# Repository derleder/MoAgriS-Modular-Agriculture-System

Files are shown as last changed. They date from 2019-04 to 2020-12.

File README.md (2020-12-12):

# MoAgriS - Modular Agriculture System

## Introduction
MoAgriS is a System to automate plant care with the help of modules for light, water and wind. The modules are plugged onto 3 rods providing power and communication. This way they can be placed individually to fit the plants needs. The project has been developed under Windows but the use of Linux is possible and encouraged.

## Quickstart
There is none. You need to get the PCBs and the components of the [BOM](#bom) first and combine them yourself or let your provider populate everything. [LCSC](https://lcsc.com/) has been quite usefull since they offer a [PCB service](https://jlcpcb.com/) besides the components and the shipment can be combined. A possible PCB configuration can be seen in [PCB/notes/pcb-spec.PNG](./PCB/notes/pcb-spec.PNG). The default values such as PCB thickness or copper weight of 1 oz are fine, too. Unfortunately not all parts can be found there at the time of writing such as the SAMD11 or the PT4115 current regulator.

Once a PCB is ready the SAMD11 needs a [bootloader](https://github.com/mattairtech/ArduinoCore-samd/blob/master/bootloaders/zero/binaries/sam_ba_Generic_D11C14A_SAMD11C14A.bin) by [Mattairtech](https://github.com/mattairtech) to be transmitted via the SWD interface. This is a one-time procedure since the bootloader handles all the firmware updates via USB afterwards. The [Segger J-Link](https://www.segger.com/products/debug-probes/j-link/models/j-link-edu-mini/) comes in handy for that if the licensing is not a problem to you. Other solutions are possible as long as the SAMD11 is supported. Currently I use [Atmel Studio](https://www.microchip.com/mplab/avr-support/atmel-studio-7) for this step (Tools->Device Programming) though the Studio is quite an overkill.

Right now there is no Firmware binary (see [Future](#Future)) so you need to go through the [Development](#Development) section to set up the [Arduino IDE](https://www.arduino.cc/en/main/software). After that you can compile and upload the firmwares found in [Firmware](/Firmware). You need one master on the SDI bus and you can use pretty much as many slaves as you want - tell me if there's a limit. The master can be any PCB that has a SAMD11 if you wish to wish keep your order small. The dedicated master PCB only has power and BUS connectors.

Now that the PCBs are fully working it's time to clamp them on the rods. Plug the master via USB into your PC/Raspberry and open a serial console such as Realterm (Windows) or minicom (Linux). Find out the masters COM-Port (Windows: Device Manager -> COM & LPT ports -> the one thats containing Mattairtech in the description), set the Baud rate to 115200 and connect to it. You should receive a welcoming "Opening SDI-12 bus master..." the first time you connect to the master. It's best to tell your terminal to add a line feed (\n) to a command. This way the master knows to send it over the SDI bus - it's not neccessary since a command is sent anyway after a timeout of 1s.

That's it pretty much. You should be able to send commands to the individual modules now. There's a node-red solution in development to automate it further.

## Alternative Uploading
Since the USB ports are no real benefit they can be left out except for the master board which uses it for serial communication. To achieve that choose [NO_BOOTLOADER in the Arduino Tools Bootloader size menu](https://github.com/mattairtech/ArduinoCore-samd#bootloader-size-menu). After you created/exported the binaries you can use another programmer like Atmel Studio to program directly via the Segger J-Link to the very start of the flash (no address needs to be specified).

The binaries can also be found directly in the corresponding folders under Firmware.

## Development
Thanks to [Mattairtechs ArduinoCore-samd](https://github.com/mattairtech/ArduinoCore-samd) firmware development is quite easy. The setup is described [here](https://github.com/mattairtech/ArduinoCore-samd#installation) (two parts!). The flash size of the SAMD11 is quite small to fit in all the firmware but it is possible if you turn off as many functions as possible in the config.h (Windows: C:\Users\User\AppData\Local\Arduino15\packages\MattairTech_Arduino\hardware\samd\1.6.18-beta-b1\config.h). My config can be found in [Firmware/config.h](./Firmware/config.h). You will save additional flash space by setting serial config under tools to "no_uart_one_wire_one_spi".

You also need to install [Arduino-SDI-12](https://github.com/EnviroDIY/Arduino-SDI-12/releases/tag/v1.1.0) and add it to the Arduino IDE for the <SDI12.h> include. Please use v1.1.0 since newer ones do not seem to work with the SAMD11.

Additionally you should avoid costful code such as the String datatype. Right now the complete firmware for the slave takes up 10232 Bytes.

## SDI Commands
The SDI protocol consists of commands from the master and answers from the sensors in printable 7bit ACII characters. A command starts with an [address](#Addressing) followed by an instruction and an optional parameter. It is finished with an '!' and sent to the module(s). If the command is a heartbeat or a group instruction the module doesn't answer. If a certain module is addressed the answer will be given via the SDI bus starting with its address and an answer. That string is also printed to the serial if you connected the module via USB for debugging purposes.

### Addressing
The modules are addressed by a 4 character lower case hex string which represents two bytes of an SDI address. It is created during bootup in the module by xoring the 3 serial number registers of the SAMD11. Since there is no EEPROM on the controller this seems to be the best solution for getting almost unique addresses. When you install the firmware you should set up a one master one slave system to get the modules address by '?I!' and write it somewhere like the left out rectangle on the module.

Besides addressing a single module you can address multiple ones with a single command. That way you won't receive any answers from the modules though - the master will always send "ACK". The wildcard character '?' will address all modules. If an single upper case letter is used you can address groups. The default group is 'N' as in None. You can set the group of a module by sending 'abcdGL!' ('abcd' = address, 'G' = set group, 'L' = Group L). Remember there is no EEPROM so the group will be lost once the module reboots. Either write a setup routine or set SDIGROUPDEFAULT in the firmware code to keep the group after booting.

### Instructions
Commands should be finished with \n and responses are finished by \r\n by the module itself.

| Instruction | Description | Answer | Example (Command!Response) |
| --- | --- | --- | --- |
| I | Identification | abcd | ?I!abcd |
|||(Address)||
| V | Version | 00.00.02 | abcdV!abcd00.00.02 |
|||(Version)||
| Ccccc | Change address | [new Address] | abcdC1234!1234 |
|| cccc: Address |||
| H | Send Heartbeat to avoid module returning to a save state| - | ?H! |
| Jiiii | Set heartbeat interval | ACK | abcdJ0060!abcdACK |
|| iiii .. Interval in seconds (trailing 0s)
| Gc | Set SDI group | ACK | abcdGL!abcdACK
|| c: Group
| K | Get SDI group | [Group] | abcdK!abcdL
| Si | Set status LED | ACK | abcdS0!abcdACK
|| i: 0 (on), 1 (off) 
| Liii | Set power LED | ACK | abcdL100!abcdACK
|| iii: 000..255 (trailing 0s) || LL255!
| Pi | Set pump | ACK | abcdP1
|| i: 1(on), 0(off)
| Fiii | Set fan | ACK | abcdF100!abcdACK
|| iii: 000..255 (trailing 0s)

## BOM
The [BOM /PCB/notes/BOM.ods](./PCB/notes/BOM.ods) is divided into the BaseBoard which contains the components all modules share except for the Angle. Since some more parts of the BaseBoard are required for certain modules the column "See also" tells you where to look. 
There is also a [Accessories /PCB/notes/Accessories.ods](./PCB/notes/Accessories.ods) list to find some ideas about the other utensils.

## Modules
All modules are created in [Eagle](https://www.autodesk.com/products/eagle/overview) and are within the 10cm*10cm limit to use the free version.

### LED-Module 
Provides light by 3 full spectrum LEDs which intensity can be controlled via SDI. The long version has a better light and heat distribution.

### Pump-Module 
Provides water by a pump by switching it on/off via SDI. 

### Fan-Module_40mm
Provides wind by a 40mm fan that can be controlled via PWM over SDI.

### Fan-Module_80mm
Provides wind by a 80mm fan that can be controlled via PWM over SDI. This is it. That's the limit of the free Eagle version. The fuseholders sit so tightly to the fan that you might need to chop off their legs.

### SDI-Master
Optional board to be used as a SDI master. You can use any other module as a master but this one is optimized for the job. It is as slim as the LED PCB and has two possible power connectors - only use one. The screw connector also has a third terminal to also chain the BUS signal.

### Angle
Provides an ~90° angle for the rods. 

## Node-RED
You need the following plugins to make the [flow configuration in flow.json](./Node-RED/flow.json) working:

- [node-red-node-serialport](https://flows.nodered.org/node/node-red-node-serialport)
- [node-red-contrib-simple-message-queue](https://flows.nodered.org/node/node-red-contrib-simple-message-queue)

The subflow handles incoming commands or arrays of commands by means of putting them into a queue, calculating the expected response and retrying the command 3 times on false responses. It also adds "!\n" to each input so you only have to enter the pure command. The flow itself demonstrates the use of a heartbeat that beats every 10s and a setup routine that sets the heartbeat interval and the sensors' group. Additionally there is a timed injection which starts the leds at 8am and shuts them down at 5pm. After the demo setup routine you may address all the leds at once by their group address but it is not advised since you won't get an answer and so the subflow can not check if the communication worked. If there's an error you may send an email.

Node-RED MoAgriS base config

After importing the flow you need to configure the serial port by configuring the MoAgriS-Subflow (double click on the MoAgriS node -> Edit subflow template -> double click on the serial request node - it's the one after the queue).

If you wish to have a dashboard like the one below the plugin [node-red-dashboard](https://flows.nodered.org/node/node-red-dashboard) helps you.

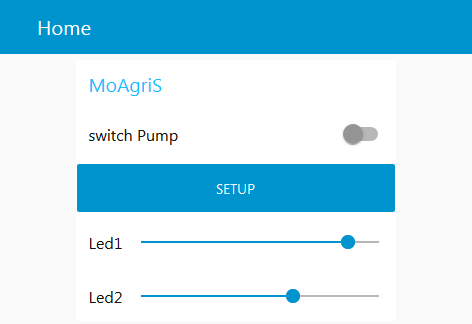
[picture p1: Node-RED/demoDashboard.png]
Node-RED MoAgriS dashboard demo


## Future
More things could be added such as
- Sensors: Currently all SDI slave boards are technically capable of driving sensors since all pins are routed outside:
	- Watering could depend on the wetness of the soil
	- Measure the water level of the pump tank to send an alert to refill
- Find an alternative to Atmel Studio for installing the bootloader
- Provide firmware binaries to avoid setting up Arduino IDE

## Bugs
- Modules don't answer after hours of no use
- Sometimes there's a voltage on the BUS of 0.1-2.5V
- Sometimes the BUS only works when a logic analyzer is attached to GND/BUS
- Sometimes it helps to connect the programmers reset pin when you need to reprogramm the bootloader

## More
<br />This work is licensed under a <a rel="license" href="http://creativecommons.org/licenses/by-sa/4.0/">Creative Commons Attribution-ShareAlike 4.0 International License</a>.

For more details see https://hackaday.io/project/91757-moagris-modular-agriculture-system

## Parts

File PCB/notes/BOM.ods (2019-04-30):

Module | See also | Qty | Component | Package | Parts | Description | URL
BaseBoard
 |  | 1 | ATSAMD11C14A-SSUT | 14-Pin SOIC | U1 | Microcontroller | https://octopart.com/atsamd11c14a-ssut-microchip-77761364?r=sp&s=35ShDJTfREeku6gmnBfHAg
 |  | 1 |  |  | D6 | Status LED | https://lcsc.com/product-detail/Light-Emitting-Diodes-LED_Red-LED-SMDLED-80-180mcd_C84256.html
 |  | 1 |  |  | R6 | Status LED Resistor R0805 | https://lcsc.com/product-detail/Chip-Resistor-Surface-Mount_Uniroyal-Elec-0805W8F590JT5E_C25274.html
 |  | 2 | 0603 Cap 1uF | 603 | C5,C6 | 0603 Cap 1uF | https://lcsc.com/product-detail/Multilayer-Ceramic-Capacitors-MLCC-SMD-SMT_SAMSUNG_CL10A105KA8NNNC_1uF-105-10-25V_C5673.html
 |  | 1 | LD1117 | SOT-223 | U3 | 3.3V LDO VREG | https://lcsc.com/product-detail/Others_STMicroelectronics_LD1117S33TR_STMicroelectronics-LD1117S33TR_C86781.html
 |  | 1 | 0805 10uF Cap | 805 | C4 | 0805 10uF Cap | https://lcsc.com/product-detail/Multilayer-Ceramic-Capacitors-MLCC-SMD-SMT_SAMSUNG_CL21A106KPFNNNE_10uF-106-10-10V_C17024.html
 |  | 1 | USB-B-MICRO-SMD |  | J1 | USB-B-MICRO-SMD | https://lcsc.com/product-detail/Micro-USB-Connectors_Korean-Hroparts-Elec-U-F-M5SW-Y-3_C106820.html
 | Angle | 3 | Fuseholder | FUSE-HOLDER-5X20MM | GND-CLIP, BUS-CLIP, VCC-CLIP | Schurter 0751.0052 or 0751.0062 | https://lcsc.com/product-detail/Fuseholders_5x20-Fuse-clip-seat_C3130.html
 |  | 1 | 2k Resistor | 1206 | R1,R3 | Resistor 2k | https://lcsc.com/product-detail/Chip-Resistor-Surface-Mount_Uniroyal-Elec-1206W4F2001T5E_C17944.html
 | LED, Pump, Fan, Master | 2 | DIODE SMA | B230A-13-F | D1, D3 | Diode | https://lcsc.com/product-detail/Schottky-Barrier-Diodes-SBD_Jiangsu-Yutai-Elec-SS23_C64990.html
 |  | 1 |  |  | F1 | Fuse | https://lcsc.com/product-detail/PTC-Resettable-Fuses_TLC-Electronic-TLC-MSMD110-24_C262027.html
LED
 |  | 1 | PCB
 |  | 1 | DIODE SMA | B230A-13-F | D2 | Diode | https://lcsc.com/product-detail/Schottky-Barrier-Diodes-SBD_Jiangsu-Yutai-Elec-SS23_C64990.html
 |  | 1 | SWPA6045S680MT | 6045 | L1 | SMT Power Inductor | https://lcsc.com/product-detail/Power-Inductors_Sunlord-SWPA6045S680MT_C53663.html
 |  | 1 | PT4115 | SOT-89-5 | IC4 | 30V, 1.2A Step-down Constant Current Driver | https://lcsc.com/product-detail/LED-Drivers_PT4115B89E-B_C15425.html https://www.ebay.de/itm/10x-PT4115-SOT89-5-Step-Down-Power-LED-Treiber-IC-30V-1-2A/173247560169
 |  | 1 | 0.33 Resistor | 1206 | R2 | Current Sense Resistor 0.33 Ohm 1% | https://lcsc.com/product-detail/Low-Resistors-Current-Sense-Resistors-Surface-Mount_KAMAYA-RLC32-R330FTP_C323760.html
 |  | 1 | Power Filter Cap | PANASONIC_C (or D=6.3mm) | C1 | Aluminum Electrolytic Capacitor 47uF | https://lcsc.com/product-detail/Aluminum-Electrolytic-Capacitors-SMD_47uF-20-25V_C141425.html
 |  | 1 | Power Filter Cap |  | C2 | Aluminum Electrolytic Capacitor 100uF | https://lcsc.com/product-detail/Aluminum-Electrolytic-Capacitors-SMD_PANASONIC-EEEFT1E101AP_C178590.html
 |  | 3 | GROW LED | LUXEON | LED-1, LED-2, LED-3 | 1W Indoor Grow LED | https://www.aliexpress.com/item/High-Power-1W-3W-5W-LED-Grow-Light-45mil-Full-Spectrum-380-840Nm-COB-SMD-Diode/32798559619.html
 |  | 3 | Heatsink |  |  | Not needed, just for testing since the center led cannot be populated with it | https://lcsc.com/product-detail/Heat-Sinks_XSD-XSD35-014_C286197.html
Pump
 |  | 1 | PCB
 |  | 1 | Pump including fixture (not quiet at all) |  |  |  | https://www.aliexpress.com/item/Ultra-quiet-DC-12V-4-2W-240L-H-Flow-Rate-Waterproof-Brushless-Pump-Mini-Submersible-Water/32956355403.html
 | Fan | 1 | 10k Resistor | 1206 | R2 |  | https://lcsc.com/product-detail/Chip-Resistor-Surface-Mount_10KR-1002-1_C104595.html
 | Fan | 1 | MOSFET | SOT23-WIDE | Q1 |  | https://lcsc.com/product-detail/MOSFET_Nexperia_PMV16XNR_Nexperia-PMV16XNR_C110920.html
 | Pump, Master | 1 | 500R | 1206 | R6 |  | https://lcsc.com/product-detail/Chip-Resistor-Surface-Mount_499R-4990-1_C102207.html
Fan
 |  | 1 | PCB
 |  | 1 | Lüfter (PCB noch ohne Kommunikation) |  |  | 40mm, 12V | https://www.aliexpress.com/item/2pcs-12V-Mini-Cooling-Computer-Fan-Small-40mm-x-10mm-DC-Brushless-2-pin-3000RPM-40/32917741685.html
 | Pump | 1 | 10k Resistor | 1206 | R2 |  | https://lcsc.com/product-detail/Chip-Resistor-Surface-Mount_10KR-1002-1_C104595.html
 | Pump | 1 | MOSFET | SOT23-WIDE | Q1 |  | https://lcsc.com/product-detail/MOSFET_Nexperia_PMV16XNR_Nexperia-PMV16XNR_C110920.html
 | Pump, Master | 1 | 500R | 1206 | R6 |  | https://lcsc.com/product-detail/Chip-Resistor-Surface-Mount_499R-4990-1_C102207.html
Master |  | 1 | Barrel Power Connector |  |  |  | https://lcsc.com/product-detail/Power-Connectors_XKB-Enterprise-DC-005-2-5A-2-0_C319099.html
 |  | 1 | 1x3 Terminal Block |  |  |  | https://lcsc.com/product-detail/Pluggable-System-Terminal-Block_METZ-CONNECT-GmbH-31060103_C123215.html
 |  | 1 | SDI Resistor | 1206 | R20 | 200k | https://lcsc.com/product-detail/Chip-Resistor-Surface-Mount_Uniroyal-Elec-1206W4J0204T5E_C37862.html
 | Pump, Fan | 2 | SDI Resistor | 1206 | R21,R22 | 510R | https://lcsc.com/product-detail/Chip-Resistor-Surface-Mount_499R-4990-1_C102207.html
 |  | 1 | SDI Cap | 603 | C20 | 3.3nF | https://lcsc.com/product-detail/Multilayer-Ceramic-Capacitors-MLCC-SMD-SMT_3-3nF-10-50V_C92203.html
Angle
 |  | 1 | PCB
 | BaseBoard | 12 | Fuseholder

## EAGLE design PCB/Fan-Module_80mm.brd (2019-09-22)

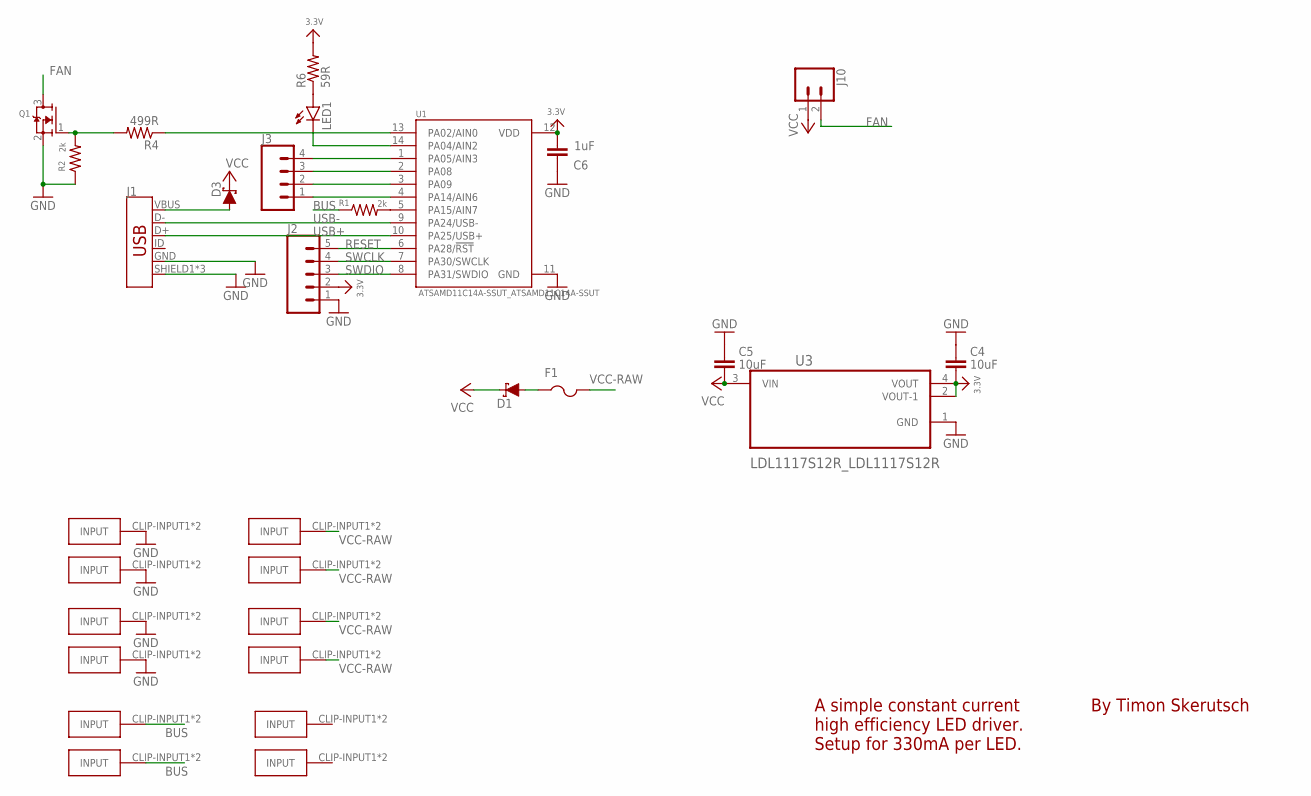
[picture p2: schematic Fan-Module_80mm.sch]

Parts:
C4, C5: 10uF; C0603
C6: 1uF; C0603
D1, D3: 3A/40V/500mV; SMA-DIODE
F1: PTCFUSE-1812; 1812
GND-CLIP, GND-CLIP1, GND-CLIP2, GND-CLIP3: FUSE-HOLDER-5X20MM
J1: USB_MICRO-B_FEMALE-SMT; USB-B-MICRO-SMD
J2: CONN_05; 1X05
J3: CONN_04PTH; 1X04
J10: CONN_02PTH3; 1X02_LONGPADS
LED1: LEDCHIPLED_0805; CHIPLED_0805
PWM-CLIP, PWM-CLIP1, PWM-CLIP2, PWM-CLIP3: FUSE-HOLDER-5X20MM
Q1: MOSFET-NWIDE; SOT23-WIDE
R1, R2: 2k; R1206
R4: 499R; R0805
R6: 59R; R0805
U1: ATSAMD11C14A-SSUT_ATSAMD11C14A-SSUT; ATSAMD11C14A-SSUT_SOIC127P600X160-14N
U3: LDL1117S12R_LDL1117S12R; LDL1117S12R_SOT230P700X180-4N
VCC-CLIP, VCC-CLIP1, VCC-CLIP2, VCC-CLIP3: FUSE-HOLDER-5X20MM

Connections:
3.3V: C4.2, C6.2, J2.2, R6.2, U1.12 (VDD), U3.2 (VOUT-1), U3.4 (VOUT)
BUS: PWM-CLIP.CLIP-INPUT1, PWM-CLIP.CLIP-INPUT2, PWM-CLIP1.CLIP-INPUT1, PWM-CLIP1.CLIP-INPUT2, R1.1
FAN: J10.2, Q1.3 (D)
GND: C4.1, C5.1, C6.1, GND-CLIP.CLIP-INPUT1, GND-CLIP.CLIP-INPUT2, GND-CLIP1.CLIP-INPUT1, GND-CLIP1.CLIP-INPUT2, GND-CLIP2.CLIP-INPUT1, GND-CLIP2.CLIP-INPUT2, GND-CLIP3.CLIP-INPUT1, GND-CLIP3.CLIP-INPUT2, J1.GND, J1.SHIELD1 (SHIELD), J1.SHIELD2 (SHIELD), J1.SHIELD3 (SHIELD), J2.1, Q1.2 (S), R2.1, U1.11 (GND), U3.1 (GND)
unnamed: LED1.C, U1.14 (PA04/AIN2)
unnamed: LED1.A, R6.1
unnamed: R1.2, U1.5 (PA15/AIN7)
unnamed: D3.A, J1.VBUS
unnamed: R4.1, U1.13 (PA02/AIN0)
unnamed: D1.A, F1.1
unnamed: J3.4, U1.1 (PA05/AIN3)
unnamed: Q1.1 (G), R2.2, R4.2
unnamed: J3.3, U1.2 (PA08)
unnamed: J3.2, U1.3 (PA09)
unnamed: J3.1, U1.4 (PA14/AIN6)
RESET: J2.5, U1.6 (PA28/!RST)
SWCLK: J2.4, U1.7 (PA30/SWCLK)
SWDIO: J2.3, U1.8 (PA31/SWDIO)
USB+: J1.D+, U1.10 (PA25/USB+)
USB-: J1.D-, U1.9 (PA24/USB-)
VCC: C5.2, D1.C, D3.C, J10.1, U3.3 (VIN)
VCC-RAW: F1.2, VCC-CLIP.CLIP-INPUT1, VCC-CLIP.CLIP-INPUT2, VCC-CLIP1.CLIP-INPUT1, VCC-CLIP1.CLIP-INPUT2, VCC-CLIP2.CLIP-INPUT1, VCC-CLIP2.CLIP-INPUT2, VCC-CLIP3.CLIP-INPUT1, VCC-CLIP3.CLIP-INPUT2

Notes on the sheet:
By Timon Skerutsch
A simple constant current high efficiency LED driver. Setup for 330mA per LED.

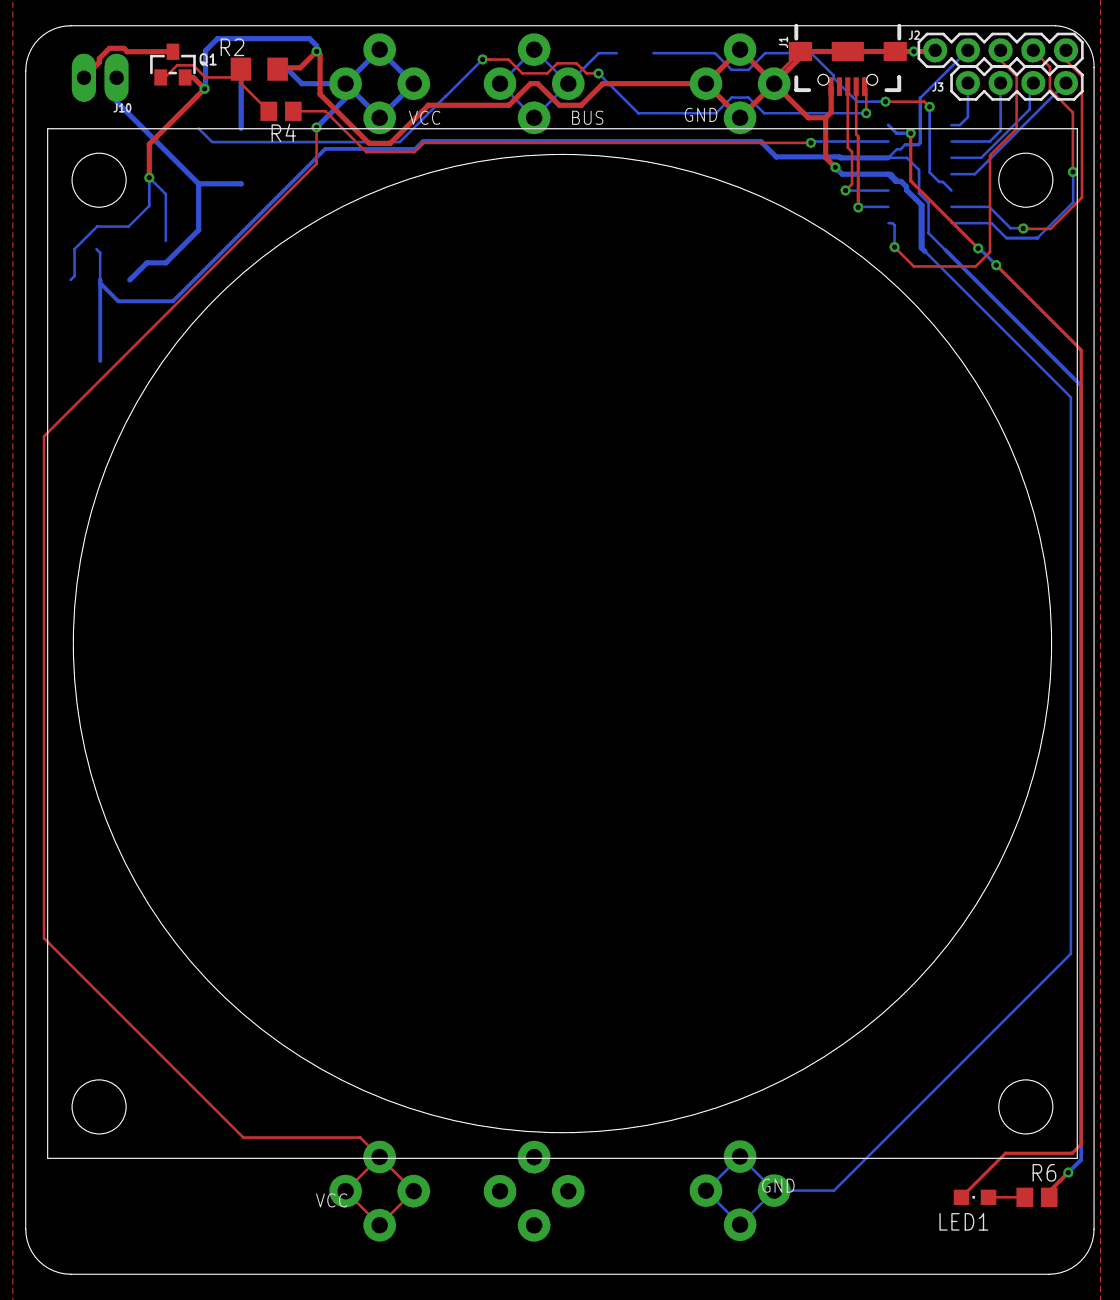
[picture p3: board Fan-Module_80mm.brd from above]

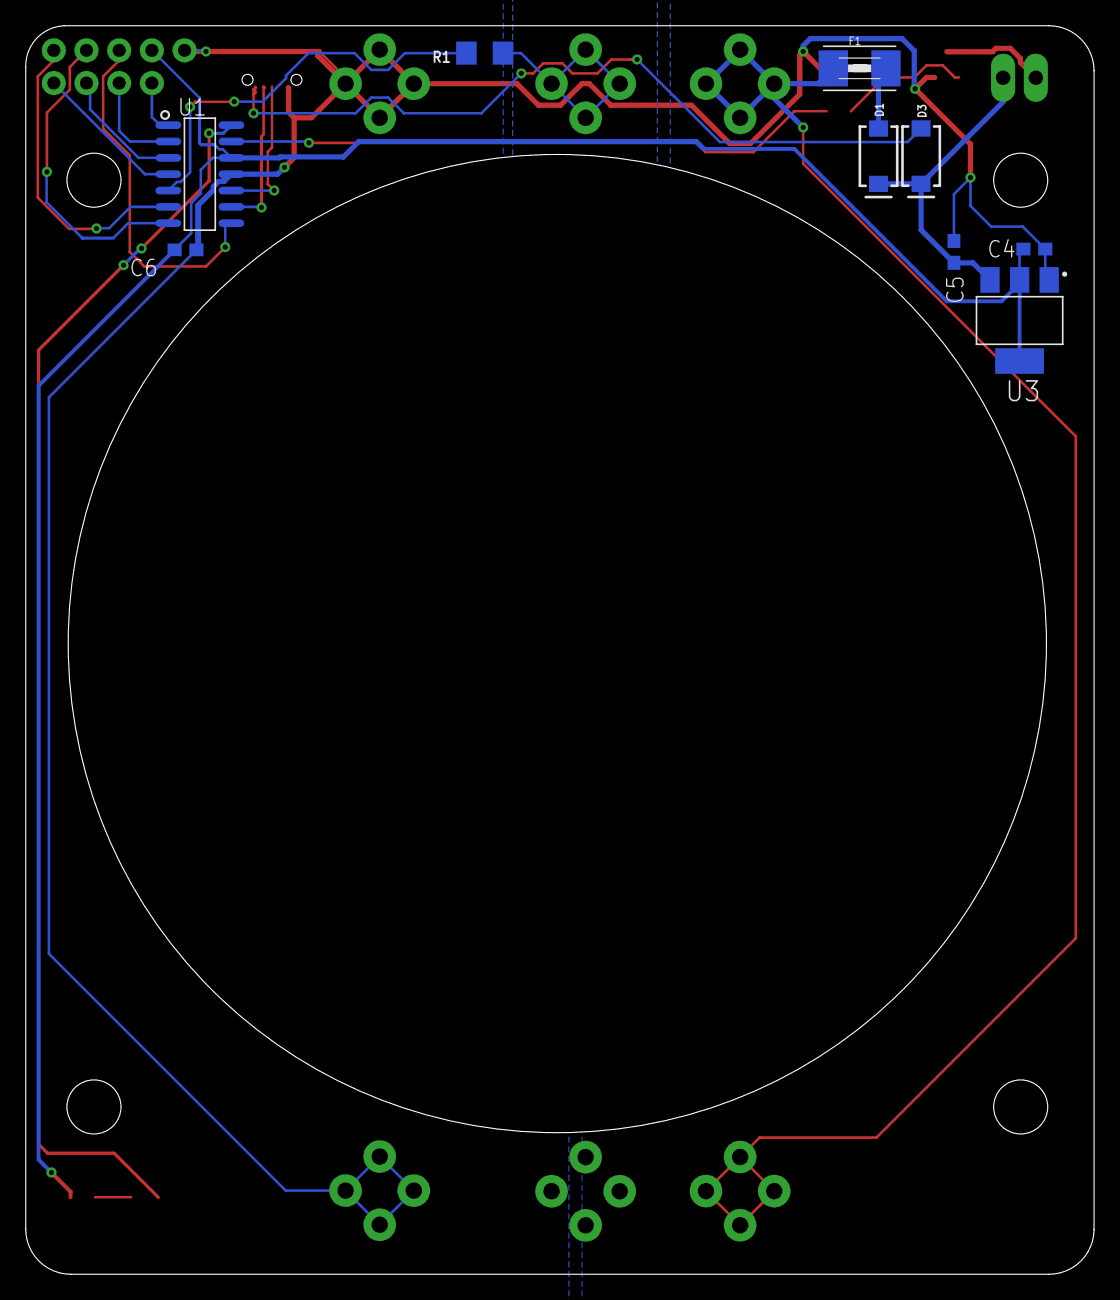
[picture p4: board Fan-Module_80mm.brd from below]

Board: 2 copper layers, 83.0 x 97.0 mm, 31 parts (10 on the bottom side), 22 nets.

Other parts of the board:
U10: 80MM-FAN

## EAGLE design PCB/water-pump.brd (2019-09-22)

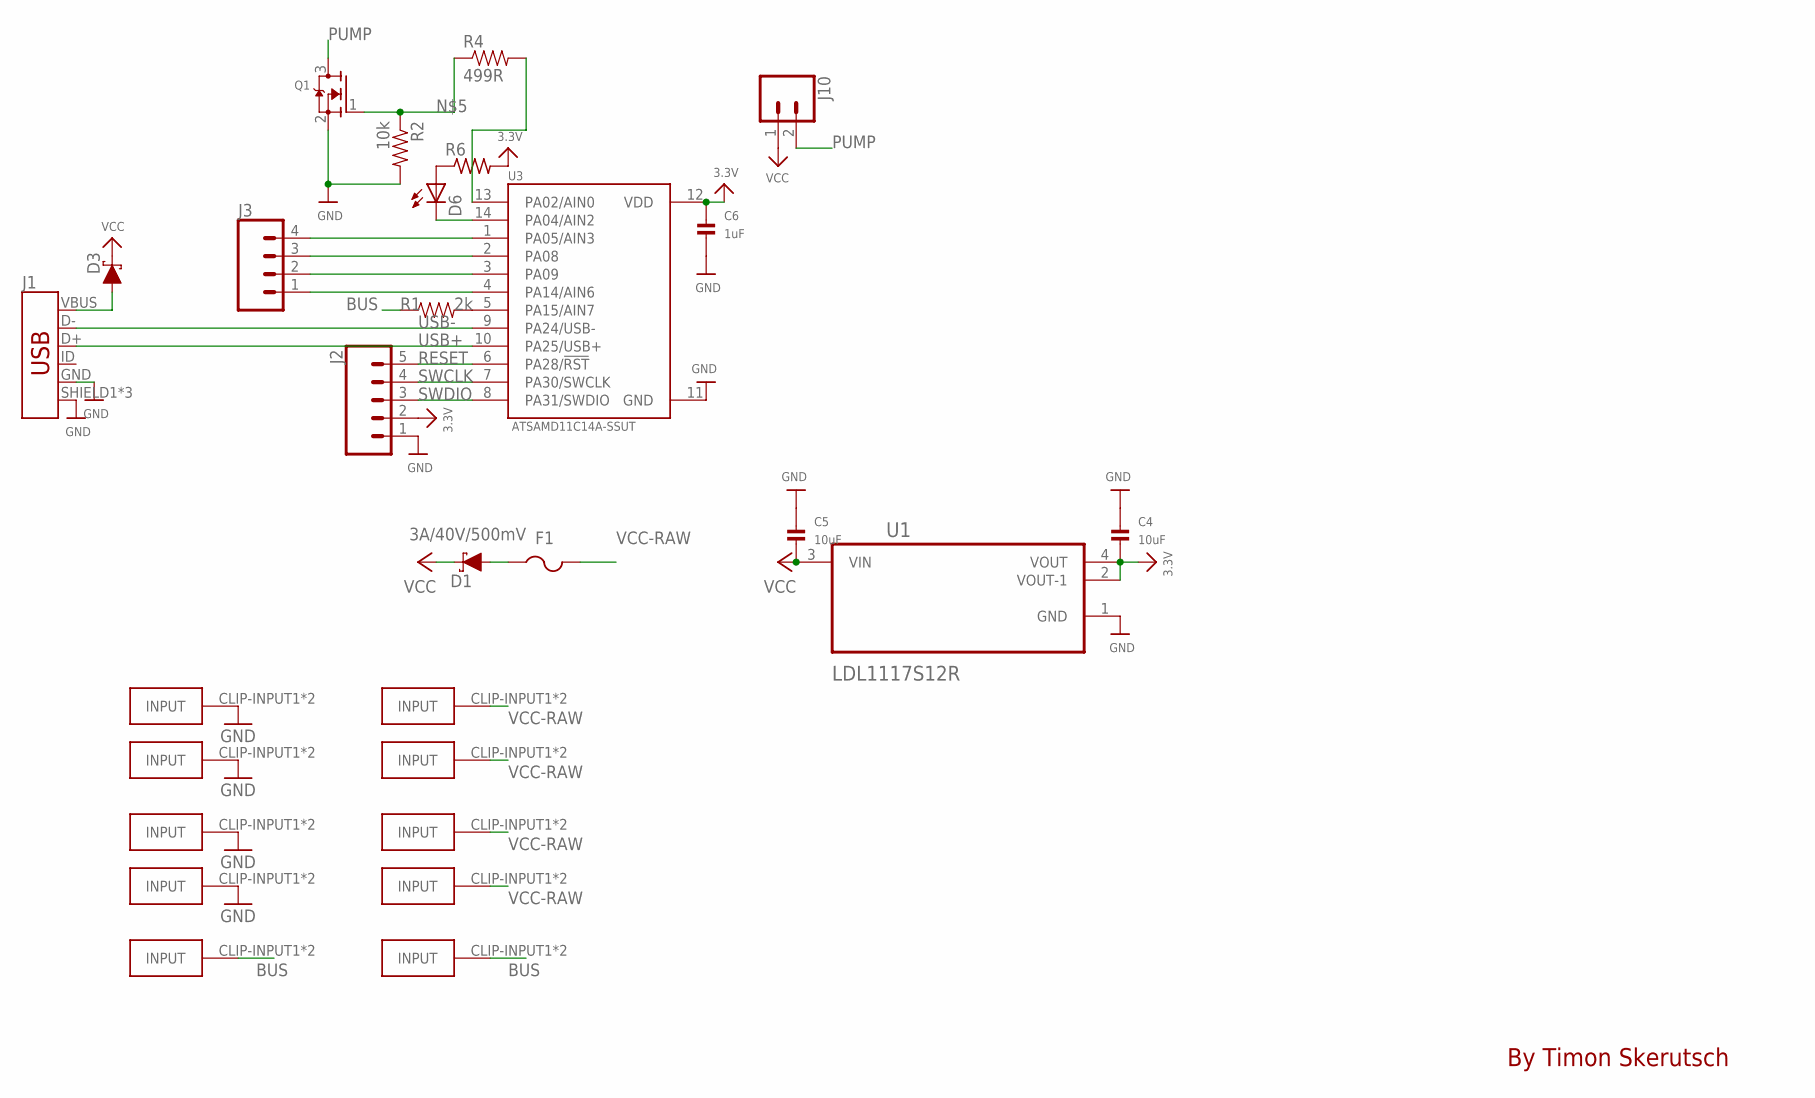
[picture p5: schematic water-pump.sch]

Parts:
C4, C5: 10uF; 0805
C6: 1uF; 0603
D1, D3: 3A/40V/500mV; SMA-DIODE
D6: LEDCHIPLED_0805; CHIPLED_0805
F1: PTCFUSE-1812; 1812
GND-CLIP, GND-CLIP1, GND-CLIP2, GND-CLIP3: FUSE-HOLDER-5X20MM
J1: USB_MICRO-B_FEMALE-SMT; USB-B-MICRO-SMD
J2: CONN_05; 1X05
J3: CONN_04PTH; 1X04
J10: CONN_02PTH3; 1X02_LONGPADS
PWM-CLIP, PWM-CLIP1: FUSE-HOLDER-5X20MM
Q1: MOSFET-NWIDE; SOT23-WIDE
R1: 2k; 1206
R2: 10k; 1206
R4: 499R; 1206
R6: R-US_R0805; R0805
U1: LDL1117S12R; SOT230P700X180-4N
U3: ATSAMD11C14A-SSUT; SOIC127P600X160-14N
VCC-CLIP, VCC-CLIP1, VCC-CLIP2, VCC-CLIP3: FUSE-HOLDER-5X20MM

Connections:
3.3V: C4.2, C6.1, J2.2, R6.2, U1.2 (VOUT-1), U1.4 (VOUT), U3.12 (VDD)
BUS: PWM-CLIP.CLIP-INPUT1, PWM-CLIP.CLIP-INPUT2, PWM-CLIP1.CLIP-INPUT1, PWM-CLIP1.CLIP-INPUT2, R1.1
GND: C4.1, C5.1, C6.2, GND-CLIP.CLIP-INPUT1, GND-CLIP.CLIP-INPUT2, GND-CLIP1.CLIP-INPUT1, GND-CLIP1.CLIP-INPUT2, GND-CLIP2.CLIP-INPUT1, GND-CLIP2.CLIP-INPUT2, GND-CLIP3.CLIP-INPUT1, GND-CLIP3.CLIP-INPUT2, J1.GND, J1.SHIELD1 (SHIELD), J1.SHIELD2 (SHIELD), J1.SHIELD3 (SHIELD), J2.1, Q1.2 (S), R2.2, U1.1 (GND), U3.11 (GND)
unnamed: D3.A, J1.VBUS
unnamed: R1.2, U3.5 (PA15/AIN7)
unnamed: J3.4, U3.1 (PA05/AIN3)
unnamed: Q1.1 (G), R2.1, R4.1
unnamed: D1.A, F1.1
unnamed: D6.A, R6.1
unnamed: D6.C, U3.14 (PA04/AIN2)
unnamed: J3.3, U3.2 (PA08)
unnamed: J3.2, U3.3 (PA09)
unnamed: J3.1, U3.4 (PA14/AIN6)
PUMP: J10.2, Q1.3 (D)
PUMP_CTRL: R4.2, U3.13 (PA02/AIN0)
RESET: J2.5, U3.6 (PA28/!RST)
SWCLK: J2.4, U3.7 (PA30/SWCLK)
SWDIO: J2.3, U3.8 (PA31/SWDIO)
USB+: J1.D+, U3.10 (PA25/USB+)
USB-: J1.D-, U3.9 (PA24/USB-)
VCC: C5.2, D1.C, D3.C, J10.1, U1.3 (VIN)
VCC-RAW: F1.2, VCC-CLIP.CLIP-INPUT1, VCC-CLIP.CLIP-INPUT2, VCC-CLIP1.CLIP-INPUT1, VCC-CLIP1.CLIP-INPUT2, VCC-CLIP2.CLIP-INPUT1, VCC-CLIP2.CLIP-INPUT2, VCC-CLIP3.CLIP-INPUT1, VCC-CLIP3.CLIP-INPUT2

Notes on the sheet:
By Timon Skerutsch

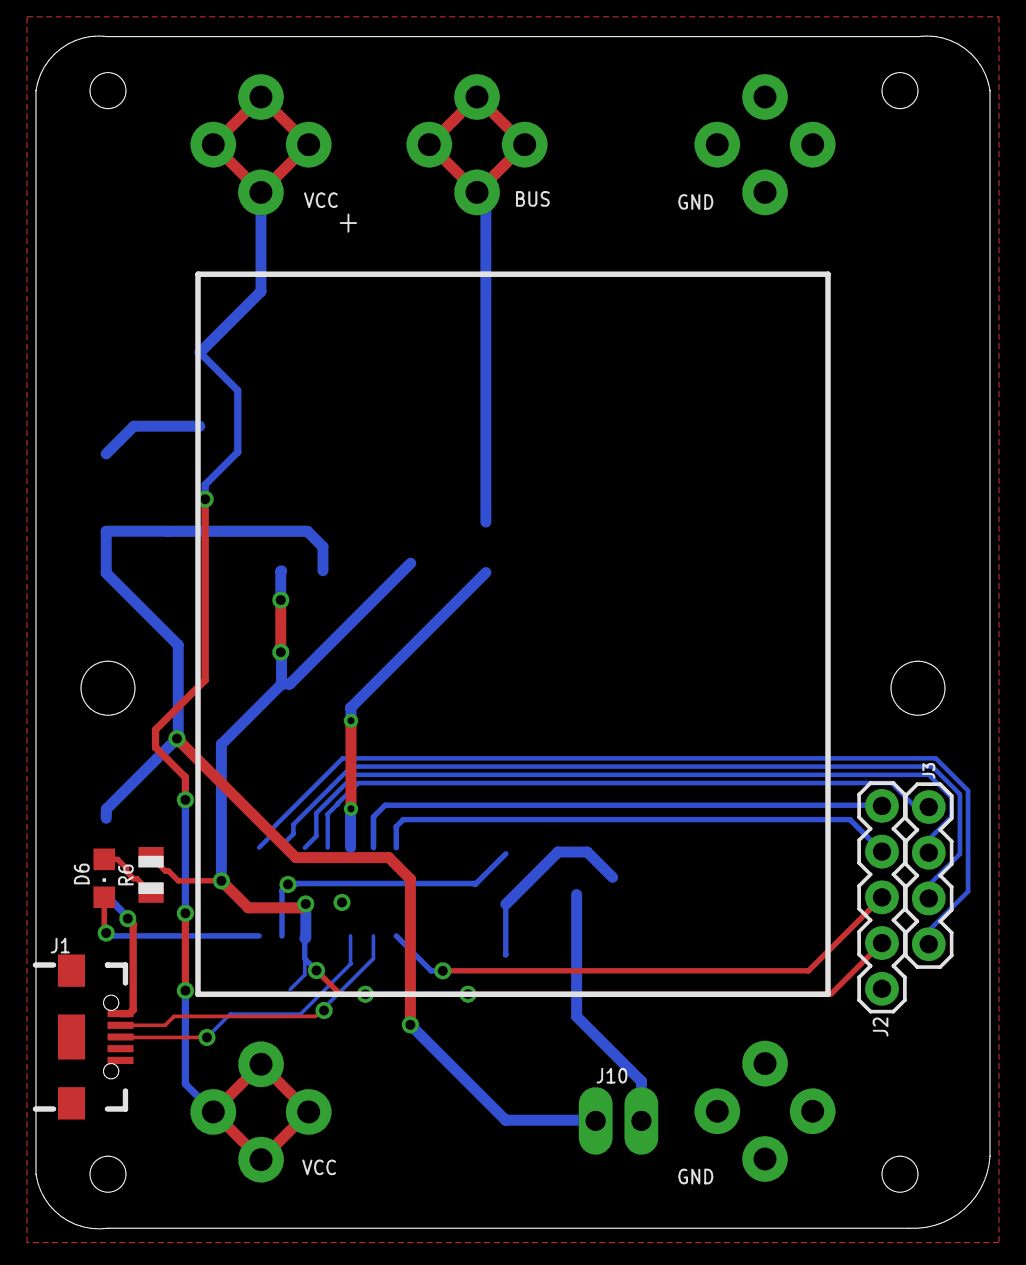
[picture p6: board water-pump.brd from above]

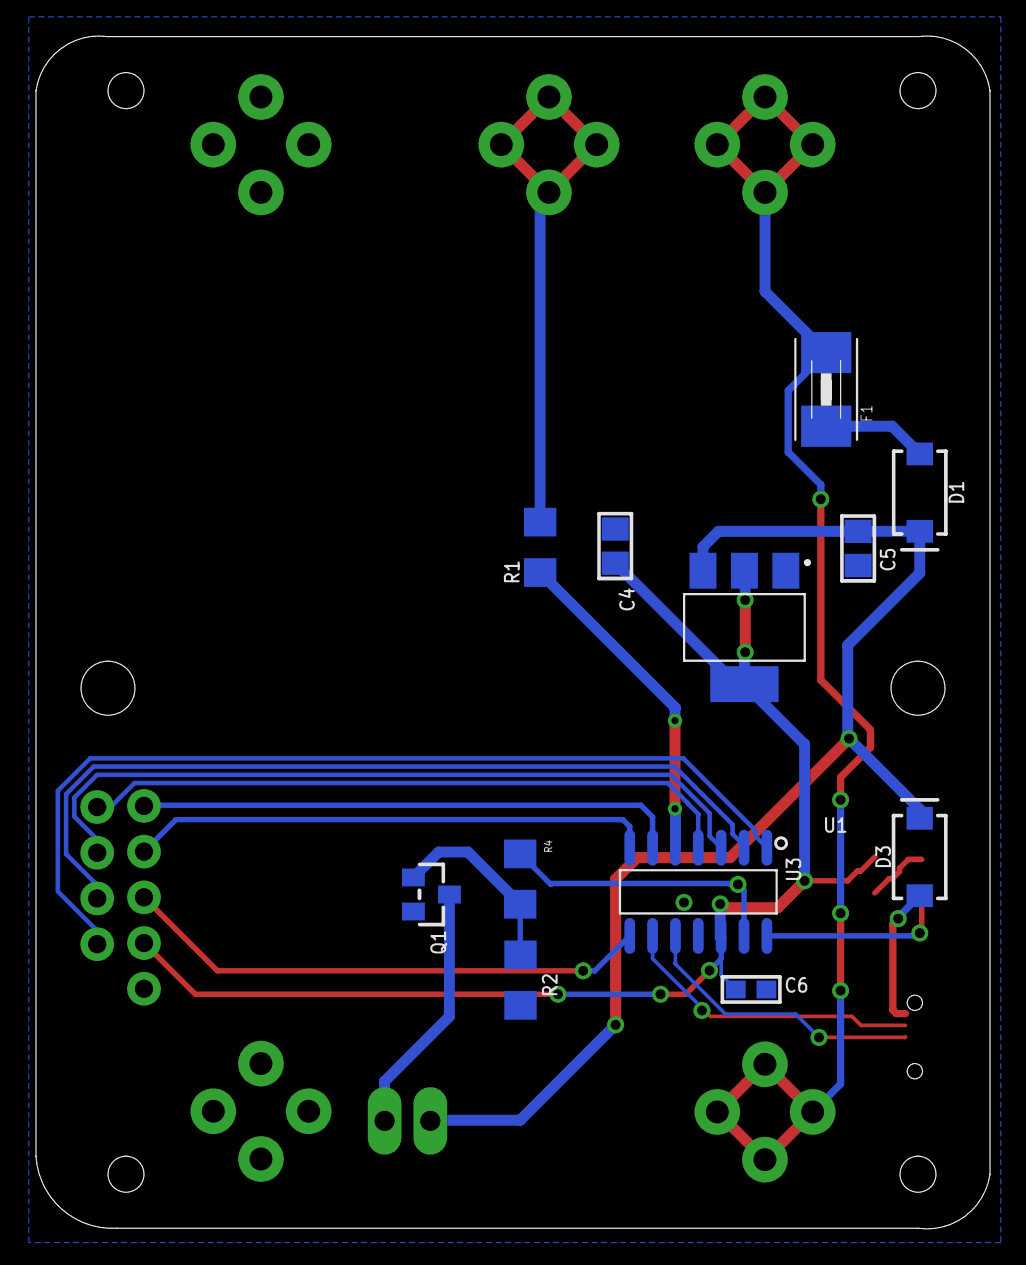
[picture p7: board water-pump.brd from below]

Board: 2 copper layers, 53.0 x 66.3 mm, 28 parts (22 on the bottom side), 22 nets.

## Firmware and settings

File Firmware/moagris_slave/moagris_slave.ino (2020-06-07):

#include <SDI12.h>

/**
   -Avoided String type since it uses way too much flash
*/

#define FIRMWAREVERSION "00.00.04"

//recommended value is 20000UL and do heartbeat every 15000ms
#define HEARTBEATINTERVAL 150543560UL //long heartbeat for development

//default time this sensor returns to safeState when actionPin has been activated by a SDI*SAFE command
#define SAFESTATEINTERVAL 10000UL //long heartbeat for development

//timeout this sensor waits for another sensors response
#define SDIWAITTIMEOUT 1000UL

//timeout this sensor waits until the cmd finishes by '!'
#define SDICMDTIMEOUT 1000UL

#define SDICMDIDENTIFICATION 'I'
#define SDICMDVERSION 'V'
#define SDICMDCHANGEADDR 'C'
#define SDICMDHEARTBEAT 'H'
#define SDICMDSETHEARTBEATINTERVALL 'J'
#define SDICMDSETSDIGROUP 'G'
#define SDICMDGETSDIGROUP 'K'
#define SDICMDSTATUSLED 'S'
#define SDICMDPOWERLED 'L'
#define SDICMDPUMP 'P'
#define SDICMDPUMPSAFE 'W'
#define SDICMDFAN 'F'

//Groups must be upper case
#define SDIGROUPNONE 'N'
#define SDIGROUPDEFAULT SDIGROUPNONE

#define LED_PIN 4           //status led
#define ACTION_PIN 2        //pump,powerled
#define DATA_PIN 15         //SDI-12 data bus



#define WAIT 0
#define INITIATE_CONCURRENT 1
#define INITIATE_MEASUREMENT 2

#define SDICMDSIZE 20
#define RESPONSESIZE 40

#define RESPENDSIZE 3
#define RESPEND "\r\n\0"

// Create object by which to communicate with the SDI-12 bus on SDIPIN
SDI12 slaveSDI12(DATA_PIN);

union unionSensorAddress {
  uint16_t w;
  char c[2];
  byte b[2];
} uSensorAddress;

union unionResponse {
  char c[RESPONSESIZE]; //whole response as char
  struct structSdiResponse {
    char address[4];
    char responseContent[RESPONSESIZE - sizeof(unionSensorAddress)];
  } sdiResponse;
} uResponse;

//static String commandReceived = "";  // String object to hold the incoming command; code with string type would use ~ 800Bytes!
static char commandReceived[SDICMDSIZE];
static char *commandWritePtr;
static char *commandReadPtr;
static bool sdiWaitUntilFinish = false;
static unsigned long sdiWaitTimeoutMillis = 0; //millis for timer to timeout waiting for other sensor to finish command
static unsigned long sdiCmdErrorTimeoutMillis = 0; //millis for timer to timeout if sensor waits too long for an finished cmd ('!')
static unsigned long hbPreviousMillis = millis(); //milliSeconds for heartbeat
static unsigned long ssStartMillis = millis(); //milliSeconds for SDI*SAFE cmd
static unsigned long hbInterval = HEARTBEATINTERVAL; //Interval to declare heartbeat missing; hold in ram to make it mutable via sdi 
static unsigned long ssInterval = SAFESTATEINTERVAL; //Interval to return to safeState when ActionPin has been activated; hold in ram to make it mutable via sdi 
static bool hbAvailable = true; //heartbeatflag
static bool ssSafeCmdActivated = false; //set true when a SDI*SAFE cmd has been sent
static bool actionPinDigitalMode= true; //mixing analog and digital mode might be a problem - fixing it that way
static char sdiGroup = SDIGROUPDEFAULT;
static byte sdiCntCharsReceived=0;



//helper function for hex codes
byte ctob(char c) {
  if (c >= '0' && c <= '9')
    return c - '0';
  //return c-48;
  else if (c >= 'a' && c <= 'f')
    return c - 87; //-'a'-10
  else
    return 0;
}
char btoc(byte b) {
  if (b < 10)
    return b + '0';
  else if (b >= 10 && b < 17)
    return b + 87;
  else
    return 0;
}

//adds \r\n\0 to response at given address
void finishResponse(char* start) {
  strncpy(start, RESPEND, 3);
}

//resets the sensor to a save state (shut down power LED/pump/fan)
void setSafeState() {
  if(actionPinDigitalMode){
    digitalWrite(ACTION_PIN, LOW);
  }else{
    analogWrite(ACTION_PIN, 0);
  }
  ssSafeCmdActivated=false;
  digitalWrite(LED_PIN, HIGH);
}



void resetSdiBuffer() {
  memset(commandReceived, 0, SDICMDSIZE);
  commandWritePtr = commandReceived;
  commandReadPtr = commandReceived;
  slaveSDI12.clearBuffer();
  sdiCntCharsReceived=0;
}

void setup() {
  setSafeState();
  pinMode(LED_PIN, OUTPUT);
  pinMode(ACTION_PIN, OUTPUT);
  Serial.begin(115200);
  //while(!Serial);

  //getting address by serialnumber
  //2 byte of 4 xored serial number words
  uSensorAddress.w = ((pgm_read_word(0x0080A00C) ^ pgm_read_word(0x0080A040)) ^ pgm_read_word(0x0080A044)) ^ pgm_read_word(0x0080A048);
  //while(!Serial);
  Serial.print("Opening SDI-12 bus slave ");
  Serial.print(btoc(uSensorAddress.c[0] & 0xf));
  Serial.print(btoc((uSensorAddress.c[0] & 0xf0) >> 4));
  Serial.print(btoc(uSensorAddress.c[1] & 0xf));
  Serial.println(btoc((uSensorAddress.c[1] & 0xf0) >> 4));
  slaveSDI12.begin();
  delay(500);
  slaveSDI12.forceListen();  // sets SDIPIN as input to prepare for incoming message
  resetSdiBuffer();
}


void loop() {

  //unsigned long hbCurrentMillis = millis(); //current millis for heatbeat


  //if sensor is waiting and timeout occurs then reset buffer
  if (sdiWaitUntilFinish && (millis() - sdiWaitTimeoutMillis) >= SDIWAITTIMEOUT) {
    //Serial.print("timeout: ");Serial.print(millis());Serial.print("-");Serial.println(sdiWaitTimeoutMillis);
    sdiWaitUntilFinish = false;
    resetSdiBuffer();
  }

  if(sdiCntCharsReceived>0 && (millis()-sdiCmdErrorTimeoutMillis) >= SDICMDTIMEOUT){
    resetSdiBuffer();
  }

  int avail = slaveSDI12.available();
  if (avail < 0) {
    slaveSDI12.clearBuffer(); // Buffer is full; clear
  } else if (avail > 0) {
    for (int a = 0; a < avail; a++) {
      char charReceived = slaveSDI12.read();

      //null seems to be a character - ignore it
      if(charReceived == 0){
        continue;
      }

      //set timer to timeout if sensor waits too long for an finished cmd ('!')
      if(sdiCntCharsReceived==0 ){
        sdiCmdErrorTimeoutMillis=millis();  
      }
      sdiCntCharsReceived++;
      
      //Serial.print("charReceived:"); Serial.println(charReceived);
      // Append command string with new character
      *commandWritePtr = charReceived; //TODO check too long command
  
      
      //if sensor is waiting and the other sensor finished its command then reset buffer
      if (sdiWaitUntilFinish && *(commandWritePtr - 1) == '\r' && *(commandWritePtr) == '\n') {
        sdiWaitUntilFinish = false;
        resetSdiBuffer();
        continue; //no command can be sent in between so we can continue here
      }
      
      commandWritePtr++;

      // Character '!' indicates the end of an SDI-12 command; if the current
      // character is '!', stop listening and respond to the command
      if (charReceived == '!') {
        unionSensorAddress uCmdAddr;
        bool isGroupCmd = false;

        //Either first char is wildcard ? or an upper case letter for group A-Z
        //or the first 4 chars are address
        if (*commandReadPtr == '?' || (commandReceived[0] >= 'A' && commandReceived[0] <= 'Z')) {
          //Serial.print("b.0");
          isGroupCmd = true;
          if (*commandReadPtr == '?' || *commandReadPtr == sdiGroup) {
            uCmdAddr.w = uSensorAddress.w;
          }
          commandReadPtr++;
        } else {
          //convert address
          uCmdAddr.b[0] = (ctob(commandReceived[1]) << 4) + ctob(commandReceived[0]);
          uCmdAddr.b[1] = (ctob(commandReceived[3]) << 4) + ctob(commandReceived[2]);
          commandReadPtr += 4;
        }

        //only act if command is not a heartbeat
        if (*commandReadPtr != SDICMDHEARTBEAT) {
          //only if this sensor is addressed by wildcard or sensorAddress
          if (uCmdAddr.w == uSensorAddress.w) {
            uResponse.sdiResponse.address[0] = btoc(uSensorAddress.c[0] & 0xf);
            uResponse.sdiResponse.address[1] = btoc((uSensorAddress.c[0] & 0xf0) >> 4);
            uResponse.sdiResponse.address[2] = btoc(uSensorAddress.c[1] & 0xf);
            uResponse.sdiResponse.address[3] = btoc((uSensorAddress.c[1] & 0xf0) >> 4);

            byte finishOffset = 0;
            byte intensity = 0;
            char sdiCommand=*commandReadPtr++;
            switch (sdiCommand) { //if/elseif instead of switch would save 8 bytes
              case SDICMDIDENTIFICATION: //xored serial number of samd11; blank responseContent
                finishOffset = 0;
                break;
              case SDICMDVERSION:
                strcpy(uResponse.sdiResponse.responseContent, FIRMWAREVERSION);
                finishOffset = sizeof(FIRMWAREVERSION);
                break;
              case SDICMDSTATUSLED: // set status LED to value (char) [S]
                digitalWrite(LED_PIN, ctob(*commandReadPtr));
                strcpy(uResponse.sdiResponse.responseContent, "ACK");
                finishOffset = 3;
                break;
              case SDICMDFAN:  // set fan to value (char)
              case SDICMDPOWERLED: // set powerled to value (char)
                //chars 2..4 are acii coded values between 000..255 (leading 0s); not using atoi since it uses 500bytes
                intensity = 0xff & ((byte)(*commandReadPtr++ - '0') * 100 + (byte)(*commandReadPtr++ - '0') * 10 + (byte)(*commandReadPtr++ - '0')); 
                analogWrite(ACTION_PIN, intensity); //uses ~550 Bytes!
                actionPinDigitalMode=false;
                strcpy(uResponse.sdiResponse.responseContent, "ACK");
                finishOffset = 3;
                break;
              case SDICMDPUMP: // set pump to value (char)
                digitalWrite(ACTION_PIN, ctob(*commandReadPtr));
                actionPinDigitalMode=true;
                strcpy(uResponse.sdiResponse.responseContent, "ACK");
                finishOffset = 3;
                break;
              case SDICMDPUMPSAFE: // activates ACTION_PIN (1) and reads time in s to return to safeState
                ssInterval = (*commandReadPtr++ - '0') * 1000 + (*commandReadPtr++ - '0') * 100 + (*commandReadPtr++ - '0') * 10 + (*commandReadPtr++ - '0'); //command must have 4 chars of value (leading 0s if necessary)
                ssInterval*=1000;
                ssSafeCmdActivated=true;
                ssStartMillis = millis();
                digitalWrite(ACTION_PIN, HIGH);
                actionPinDigitalMode=true;
                strcpy(uResponse.sdiResponse.responseContent, "ACK");
                finishOffset = 3;
                break;
              case SDICMDSETHEARTBEATINTERVALL: //set new heartbeat intervall in s
                hbInterval = (*commandReadPtr++ - '0') * 1000 + (*commandReadPtr++ - '0') * 100 + (*commandReadPtr++ - '0') * 10 + (*commandReadPtr++ - '0'); //command must have 4 chars of value (leading 0s if necessary)
                hbInterval*=1000;
                strcpy(uResponse.sdiResponse.responseContent, "ACK");
                finishOffset = 3;
                break;
              case SDICMDSETSDIGROUP:
                sdiGroup = *commandReadPtr;
                strcpy(uResponse.sdiResponse.responseContent, "ACK");
                finishOffset = 3;
                break;
              case SDICMDGETSDIGROUP:
                *uResponse.sdiResponse.responseContent=sdiGroup;
                finishOffset=1;
                break;
              default:
                strcpy(uResponse.sdiResponse.responseContent, "NAK");
                finishOffset = 3;
                break;
            }

            //sending via sdi if it's not a group command
            if (!isGroupCmd || sdiCommand==SDICMDIDENTIFICATION) {
              finishResponse((uResponse.sdiResponse.responseContent + finishOffset));
              slaveSDI12.sendResponse(uResponse.c);
            } else {
              Serial.print("Not sent on sdi since group cmd: "); //little serial helper text
              isGroupCmd = false;
            }
            Serial.print(uResponse.c);
            
            //reset command and ptr
            resetSdiBuffer();
          } else {
            //start listening to \r\n and start timeout timer to reset buffer
            sdiWaitUntilFinish = true;
            sdiWaitTimeoutMillis = millis();
          }
        }

        //reset heartbeat on every command, also on commands for other sensors
        hbPreviousMillis = millis(); //resets heartbeat
        hbAvailable = true; //new command resets heartbeat



      } 
    }
  }

  //when SDI*SAFE cmd is active and time passed return to safeState
  if (ssSafeCmdActivated && (millis() - ssStartMillis >= ssInterval)) { 
    setSafeState();
  }

  //Heartbeat - return to savestate if heart didn't beat in the last hbInterval
  if (hbAvailable && (millis() - hbPreviousMillis >= hbInterval)) { //only jump in here if heartbeat as been available till now (hbAvailable)
    hbAvailable = false;
    setSafeState();
  }
  
}

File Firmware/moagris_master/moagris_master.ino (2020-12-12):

#include <SDI12.h>

#define SERIAL_BAUD 115200  // The baud rate for the output serial port
#define DATA_PIN 15         // The pin of the SDI-12 data bus
#define LED_PIN 4

#define ACTION_PIN 2        //pump,powerled
// Define the SDI-12 bus

SDI12 mySDI12(DATA_PIN);

/*
  '?' is a wildcard character which asks any and all sensors to respond
  'I' indicates that the command wants information about the sensor
  '!' finishes the command
*/
String myCommand = "?HELLOSLAVE!";

/*
 * set safe state even if its the sdi master; otherwise normal pcbs might turn on the action
 */
void setSafeState(){
  digitalWrite(ACTION_PIN,LOW);
  digitalWrite(LED_PIN,HIGH);
}

void setup(){
  setSafeState();
  pinMode(LED_PIN, OUTPUT);
  pinMode(ACTION_PIN, OUTPUT);
  
  Serial.begin(SERIAL_BAUD);
  while(!Serial);

  Serial.println("Opening SDI-12 bus master...");
  mySDI12.begin();
  delay(500); // allow things to settle
}

void loop(){
  /*
  mySDI12.sendCommand(myCommand);
  delay(100);                     // wait a while for a response
  while(mySDI12.available()){    // write the response to the screen
    Serial.write(mySDI12.read());
  }
  */
  if (Serial.available() > 0) {
    digitalWrite(4, LOW);
    
    /*
    while(Serial.available() > 0) {
      char t = Serial.read();
      Serial.print(t);
    }*/

    
    myCommand=Serial.readStringUntil('\n');
    
    //Serial.print("Sending ");
    //Serial.println(myCommand);
    
    mySDI12.sendCommand(myCommand);
    delay(100);                     // wait a while for a response
    if (myCommand[1] != 'I' && (myCommand[0] == '?' || (myCommand[0] >= 'A' && myCommand[0] <= 'Z'))) {
      //no answer expected
      Serial.print("ACK\r\n");
    }
    else if(mySDI12.available()){
      while(mySDI12.available()){    // write the response to the screen
        char sdiChar=mySDI12.read();
        if(sdiChar!=127){ //remove marking if present
          Serial.print(sdiChar);
        }
        //Serial.write(mySDI12.read());
      }
      Serial.print("\r\n");
    }

  
  }
  digitalWrite(4, HIGH);
  setSafeState(); //sometimes power pin is turned on without a reason. 
}

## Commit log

2019-04-08 removed thermals from canvas to improve heat transportation to the rods
    [LED-Board.brd, LED-Board_long.brd]
2019-04-11 removed master printing incomming cmd to serial for node-red
2019-04-13 added heatsinks to bom for testing
    [BOM.ods]
2019-04-26 added 4pin connector for remaining pins on all boards
    [Fan-Module.brd, Fan-Module.sch, LED-Board.brd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]
2019-04-30 added 80mm fan and renamed small 40mm fan
    [Fan-Module_40mm.brd, Fan-Module_40mm.sch, Fan-Module_80mm.brd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]
2019-04-30 modified sdi master to suit sdi application node
    [sdi-master.brd, sdi-master.sch]
2019-04-30 updated BOM
    [BOM.ods]
2019-09-22 unknown changes, break has been too long
    [Fan-Module_80mm.brd, LED-Board_long.brd, sdi-master.brd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]
2020-06-06 added save pump command
2020-06-07 slave prints address on serial start
2020-06-07 workaround for using action pin in analog and digital mode
    [moagris_slave.ino]
2020-12-12 fixed master bug receiving address from unknown board, updated readme to program without usb port
    [moagris_master.ino]

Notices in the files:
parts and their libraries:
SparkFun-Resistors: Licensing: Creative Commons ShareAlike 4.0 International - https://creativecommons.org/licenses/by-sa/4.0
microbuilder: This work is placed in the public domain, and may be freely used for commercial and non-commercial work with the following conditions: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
